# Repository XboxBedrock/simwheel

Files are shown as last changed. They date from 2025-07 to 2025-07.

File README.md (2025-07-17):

# Custom Simracing FFB Wheel

Hi! This is a custom-made Force Feedback Simracing steering wheel, made to somewhat resemble the 2019 Mercedes AMG F1 steering wheel, although not a direct replica. It is made using a hoverboard motor to save costs, and has a screen on the controller for the true F1 experience. For those who may not know what Force Feedback is, it's the usage of a motor to resist the motion of the player, to more closely mimic racecar steering, as the steering column in a racecar offers significant resistance to the driver. Generally this results in higher steering accuracy as humans are very good at gauging pressure accurately compared to distance, so resistance from a wheel helps with that. The wheel itself has a lot of buttons, as does every F1 steering wheel, to allow the driver to enable functions like pit lane steering limiter, etc. I am using keyswitches for a nice shifter experience, and a rotary encoder clutch pedal.

The premade setups you can get at this pricepoint do not offer the same selection of button and screen, and are lacking in torque (Often 2-3 Nm), so that made me want to make a much more capable wheel. There is significant complexity as the hub, wheel, and quickconnect all have to be designed. Overall I am a simracing fan and have always wanted to have a setup like this, but have been outpriced by the $700+ market rates, and figured this could be a great way to use my cad and pcb experience.

## Software

I intend to use a mix of the OpenFFBoard project's software (https://github.com/Ultrawipf/OpenFFBoard) and a small custom serial interface for the buttons and clutch pedal. As such this means you will plug in two USB cables to the computer, one for the wheel control and one for the buttons and clutch and display controller.

## Wiring Diagram

Wiring

This is the full wiring diagram, the display unit will have 2 PCBs hooked up to it for the RPM status lights, and one to hold the shifter keyswitches (which is apart of buttons), as visible in the cad. All of the PCB design files can be found in the [kicad_project](./kicad_project/) folder. Here are the schematics and routing as images for sake of convinience however.

As to not spam this upper section with images, please check the [pcb images section](#pcb-images)

## CAD

All of the CAD was done in fusion 360, and while I *could* export my whole workspace, for the sake of sanity I uploaded the full assembly and just the wheel as two seperate files, the full assembly containing the wheel. Credit to GrabCAD for providing the models for some standard COTS parts (EG. ESP32, Power Supply, Magnetic Encoder Board, etc.).

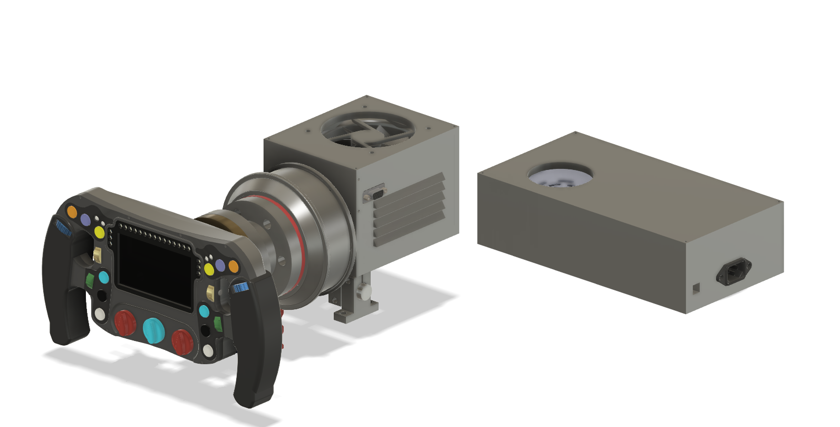
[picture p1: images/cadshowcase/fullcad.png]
full cad

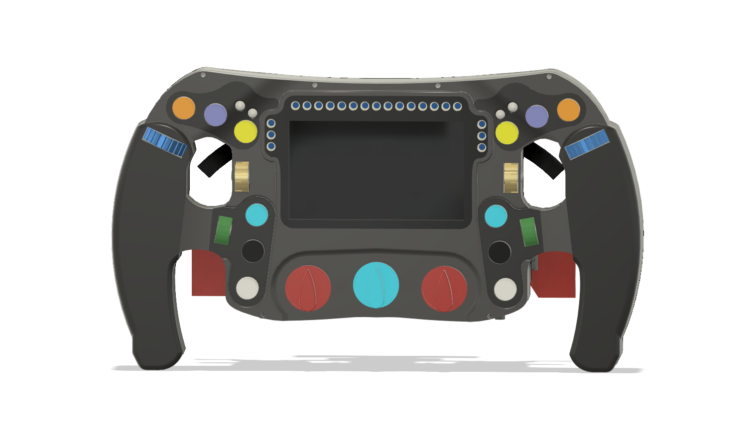
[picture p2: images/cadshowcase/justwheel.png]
Just Wheel


## BOM

|Name |Price |Qty  |Expenditure|FIELD5|Link |Notes: |
|---|---|-----|---|---|---|---|
|Hoverboard |$50 |1 |$50 | |https://www.ebay.com/itm/316843156432 | |
|Ballbearings |$5.45 |1 |$5.45 | |https://www.amazon.com/0-236-Precision-Chrome-Steel-Bearing/dp/B07L8MLK2N/ | |
|Springs |$5.30 |1 |$5.30 | |https://www.amazon.com/uxcell-Compression-Spring-Stainless-Length/dp/B0C33CQ5LN/ | |
|Tactile Switch Buttons 12mm |$0.06 |20 |$1.11 | |https://lcsc.com/product-detail/Tactile-Switches_Megastar-ZX-QC1212-7-5CJ_C7470190.html?s_z=n_12mm%2520button | |
|Rotary Encoder |$1.77 |12 |$21.24 | |https://www.digikey.com/en/products/detail/bourns-inc/PEC11R-4225F-S0024/4499659 |Not in stock on LCSC, no similar models instock either|
|Neopixel Indiv |$4.95 |1 |$4.95 | |https://www.adafruit.com/product/1938 |Only adafruit has in stock and/or sells :( |
|WS2812B |$0.05 |30 |$1.47 | |https://lcsc.com/product-detail/RGB-LEDs-Built-in-IC_XINGLIGHT-XL-5050RGBC-WS2812B_C2843785.html?s_z=n_ws2812b | |
|470 Resistor |$0.00 |100  |$0.19 | |https://lcsc.com/product-detail/Chip-Resistor-Surface-Mount_YAGEO-RC0805FR-0710KL_C84376.html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 | |
|0.1uF Cap |$0.00 |100  |$0.46 | |https://lcsc.com/product-detail/Multilayer-Ceramic-Capacitors-MLCC-SMD-SMT_YAGEO-CC0805KRX7R9BB104_C49678.html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| |
|MX Blue |$1.25 |2 |$2.50 | |https://www.digikey.com/en/products/detail/cherry-americas-llc/MX1A-E1NN/40084 |Not in stock on LCSC, no similar models instock either|
|M3 Screw Assortment |$9.99 |1 |$9.99 | |https://www.amazon.com/Assortment-Stainless-Replacement-Machine-Fastener/dp/B0BMQFHDBH/ | |
|M5 Screw + Nuts |$9.99 |1 |$9.99 | |https://www.amazon.com/Assortment-Machine-Stainless-Washers-Threaded/dp/B0DFWW9DZK/ | |
|4.3"LCD HDMI VGA,Video AV Driver Controller Board,TFT Module Display|$26.79|1 |$26.79 | |https://www.buydisplay.com/4-3-lcd-hdmi-vga-video-av-driver-controller-board-tft-module-display | |
|Carbon Fibre Sticker Wrap |$6.76 |1 |$6.76 | |https://www.aliexpress.us/item/2251832843233677.html | |
|PCB |$15 |1 |$15 | |JLCPCB Cart | |
|SK16 Linear Shaft Holders 4x |$1.18 |1 |$1.18 | |https://www.aliexpress.us/item/2255801037008492.html | |
|SK16 Linear Shaft Holders 2x |$0.99 |1 |$0.99 | |https://www.aliexpress.us/item/3256803971216207.html | |
|16mm Shaft |$7.59 |1 |$7.59 | |https://www.amazon.com/uxcell-Linear-Hardened-Printer-Machine/dp/B0F32ZJCFC | |
|MT6701 + Magnet |$0.99 |1 |$0.99 | |https://www.aliexpress.us/item/3256808951558543.html | |
|OpenFFBoard |$34 |1 |$34 | |https://www.elecrow.com/open-ffboard-stm32f407-usb-interface-only.html | |
|96mm Fan |$8.67 |1 |$8.67 | |https://www.digikey.com/en/products/detail/sunon-fans/MF92252V2-1000U-A99/7652235 |Much to my awe, digikey has it for the cheapest? |
|ODesc 4.2 |$28.99|1 |$28.99 | |https://flipsky.net/products/odesc-v4-2-24v-56v-controller | |
|600W PSU |$29.99|1 |$29.99 | |https://www.amazon.com/BOSYTRO-Switching-Universal-Regulated-Security/dp/B0C53SLDM9/ | |
|C14 Connector |$5.11 |1 |$5.11 | |https://www.digikey.com/en/products/detail/te-connectivity-corcom-filters/1-6609987-4/1306112 | |
|USBC Extension |$2 |1 |$2 | |https://www.walmart.com/ip/onn-USB-C-Extension-Cable-White-6/153042914 | |
|XT90 |11.99 |1 |11.99 | |https://www.amazon.com/Female-Connector-Silicon-RC-Battery/dp/B08L3RS5HP/ | |
|12V Step-Down |8.99  |1 |8.99 | |https://www.amazon.com/VOLRANTISE-Converter-Voltage-Regulator-Transformer/dp/B09WZ5WH8H?th=1 | |
|VGA Connector |9.99  |1 |9.99 | |https://www.amazon.com/uxcell-Connector-Terminal-Mechanical-Equipment/dp/B07LCM71MY/ | |
|VGA Cable |5.28  |1 |5.28 | |https://www.amazon.com/Pasow-Monitor-Cable-Computer-Projector/dp/B08B64KM93/ | |
|ESP32*3 |12.99 |1 |12.99 | |https://www.amazon.com/Development-ESP-WROOM-32-Bluetooth-Microcontroller-Compatible/dp/B0DSZTZKLM/ | |
| | |Total|**$330** | |Willing to incur any extra expense to myself | |

## PCB Images

**Top Lights PCB**
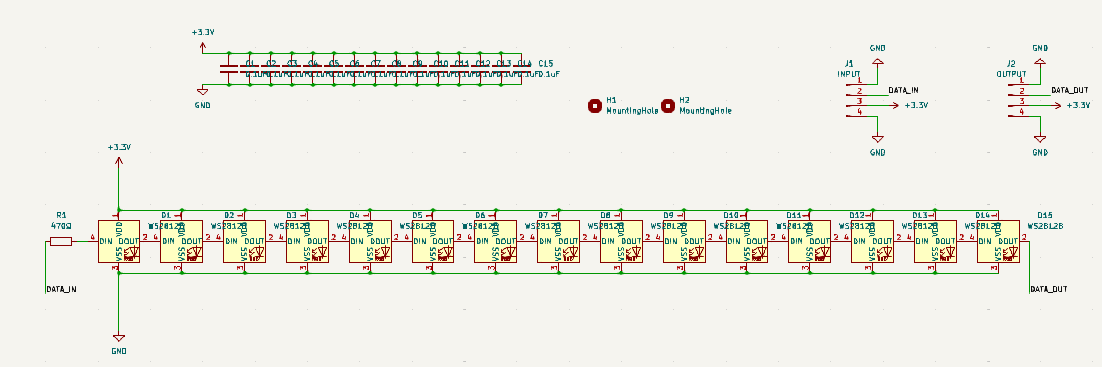
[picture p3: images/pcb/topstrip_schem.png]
Schem
 
PCB

**Safety Lights PCB**
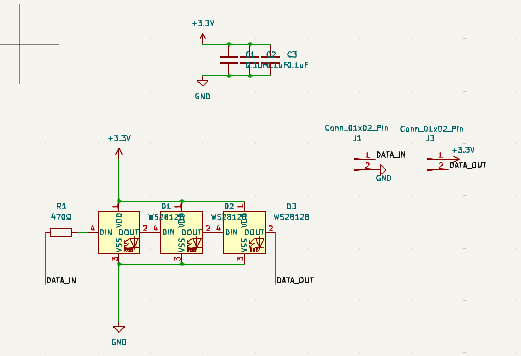
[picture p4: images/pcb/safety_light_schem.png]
Schem
 
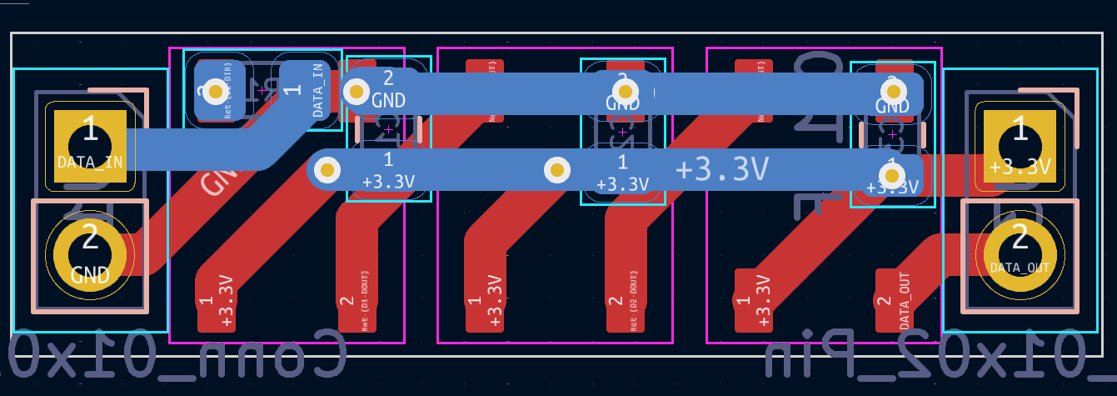
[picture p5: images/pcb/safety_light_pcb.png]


**Shifter PCB**
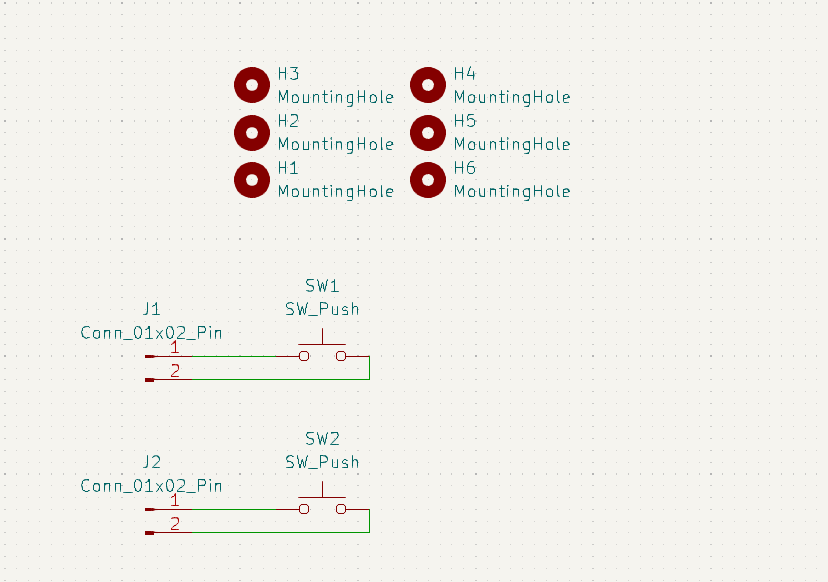
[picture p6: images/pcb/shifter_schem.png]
Schem
 
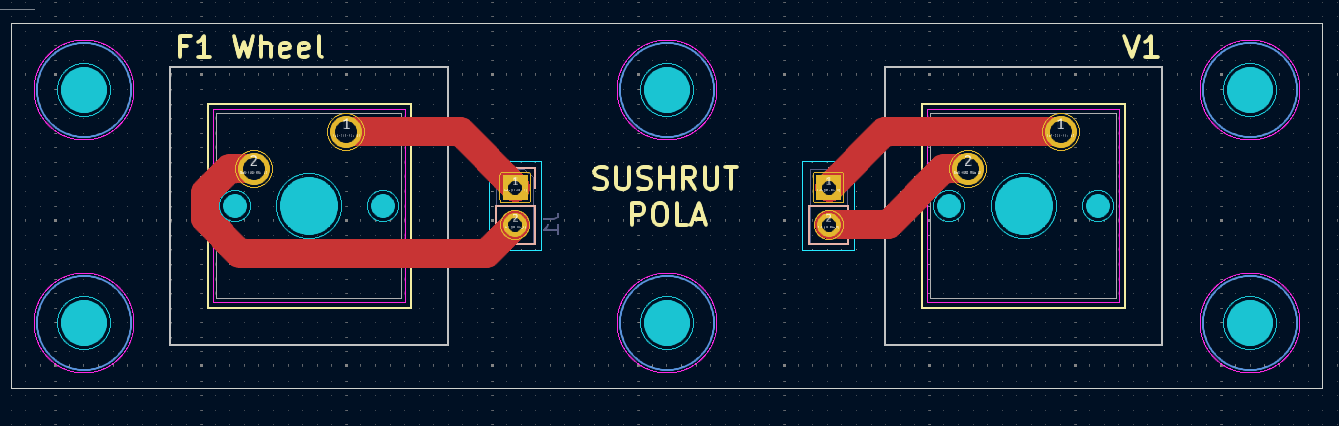
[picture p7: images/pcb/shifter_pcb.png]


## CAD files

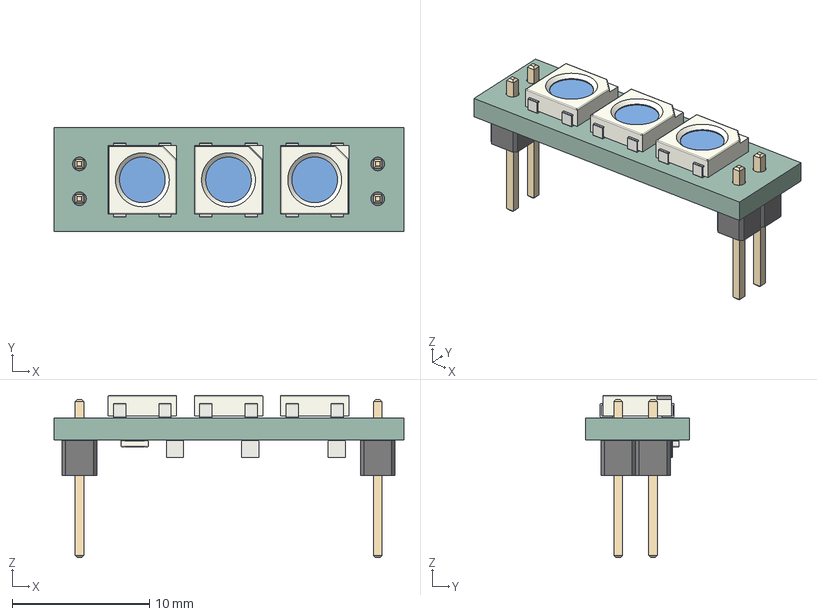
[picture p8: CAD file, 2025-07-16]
kicad_project/safety_light/safety_light/safety_light.step
25.5 x 7.57 x 11.8 mm
LED_WS2812B_PLCC4_50x50mm_P32mm x 3
C_0805_2012Metric x 3
PinHeader_1x02_P254mm_Vertical x 2
R_0805_2012Metric
safety_light_PCB

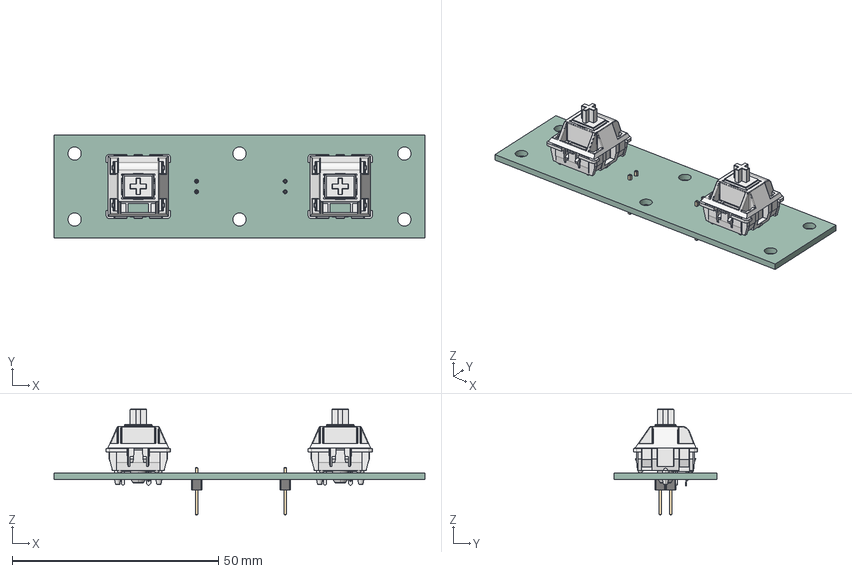
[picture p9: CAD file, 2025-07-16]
kicad_project/shifter/shifter.step
90.0 x 25.0 x 25.7 mm
ASM_MX_ASM_cp x 2
PinHeader_1x02_P254mm_Vertical x 2
shifter_PCB

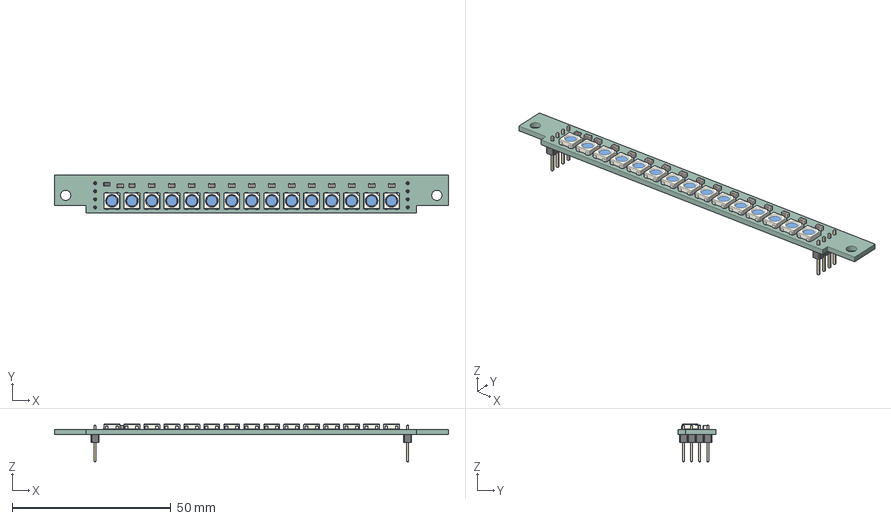
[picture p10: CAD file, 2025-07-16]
kicad_project/topstrip/topstrip.step
124.0 x 12.1 x 11.8 mm
LED_WS2812B_PLCC4_50x50mm_P32mm x 15
C_0805_2012Metric x 15
R_0805_2012Metric
PinHeader_1x04_P254mm_Vertical x 2
topstrip_PCB

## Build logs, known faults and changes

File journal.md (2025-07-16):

---
title: "Force Feedback Simracing Wheel"
author: "Sushrut Pola"
description: "A force feedback simracing steering wheel!"
created_at: "2025-06-06"
---

# Force Feedback Simracing Steering Wheel

**Total Time**: 57.5 Hours

---

Hello there, I am making a Force Feedback Steering wheel to fuel my sim racing addiction. Before I get started, you might be wondering what a "Force Feedback Steering Wheel" even is.

Normally when you turn the steering wheel in a car (even with power steering), you will feel some back force when you turn the wheel. This comes from the friction between the tires and the ground as you turn them. While this friction remains relatively the same on a given surface in a consumer car, this is not the case for racing cars.

Racing cars often use hydraulic power steering instead of electric power steering, which means you directly feel the interaction with the ground. So from how much the steering wheel resists your turning, it is reasonable for an experienced driver to deduce what surface they are on without even looking.

For Formula and Indycars, there is a concept called downforce. Downforce is the amount of force your car is pushed into the ground with. From a basic definition of friction, the more downforce (hence more normal force), the more friction between the tires and the surface. This changes the  way the steering wheel feels significantly.

When we sim race, our goal is to be able to accurately simulate the experience of being a real racecar. This can be achieved by using something called Force Feedback, where a motor attached to the steering wheel resists the motion of the wheel in order to simulate the forces you would feel in a real car.

----

*June 6th, 2025*

**Goals**:
 * Define design constraints and goals
 * Evaluate component choices
 * Possibly get started on a bit of the structural CAD

**Design Constraints**:
 * Ideally be under $350
 * Use components that ship quickly
 * Buildable in a less than 2 week timeframe
 * Is done in a safe manner (I should be confident in leaving this plugged in overnight without issue)

With this in mind, I will now move onto component choices.

In terms of the actual motor for FFB, I believe a hoverboard motor is the best option, this is largely due to its low price for being able to do nearly 15 Nm of torque. This will probably be a dumpster find or ebay find.

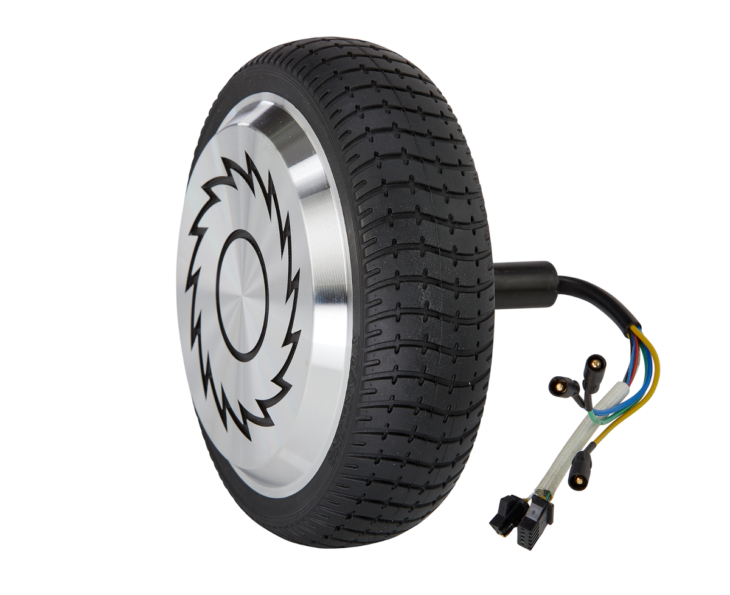
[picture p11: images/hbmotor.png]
A Hoverboard Hub Motor


<i><sup>A hoverboard hub motor<sup></i>

The rest of the parts for the base are largely low cost minutia, mostly 3D printed or standard hardware. However, I do want to use a quick-connect steering hub adapter. This allows for me to switch between wheels, but also requires me to devise a mechanism to quick-disconnect the screen and button cable. That however is a problem for another day. 

In terms of the screen however, I think a 3.5" LCD best suits the f1 style wheel I want. Buttons and switches are fairly COTS components that are easy to find at low cost.

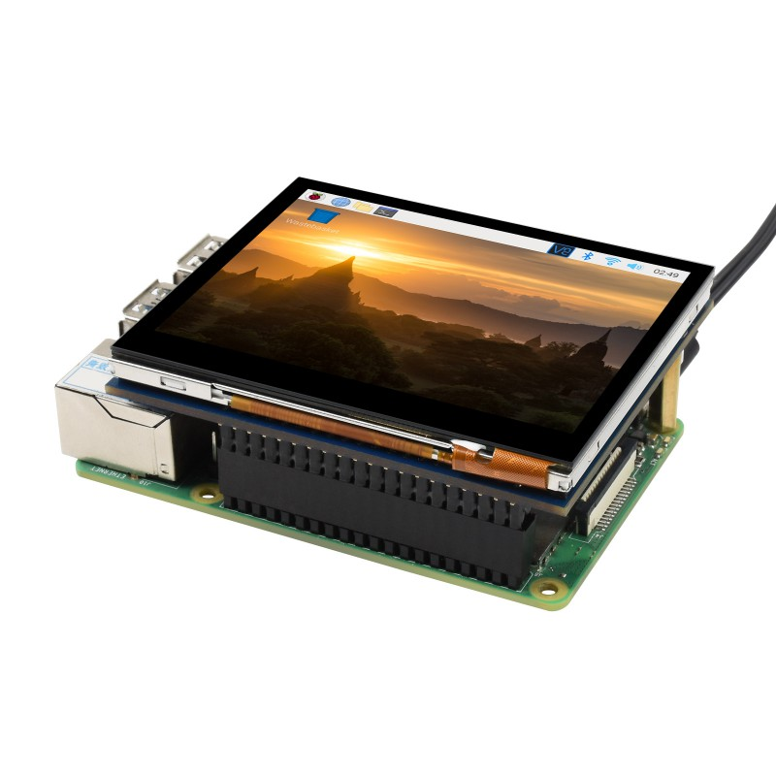
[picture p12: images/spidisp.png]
SPIDISP


<i><sup>A SPI display similar to the one I want to use, they come really cheap<sup></i>

There are some electronic design choices that need to be made, but due to lack of time I will likely do that later.

**Time Spent: 4h**

---

*June 7th, 2025*

One thing this steering wheel needs is a quick connect mechanism. This quick-connect mechanism is what connects the steering wheel to the driver shaft in a manner that can be easily removed. This is very common in racecars and will allow me to easily swap out the wheel later. It will need some 6mm ball bearings for the latch mechanism.

The way it works is a bit convoluted, but in a simple manner there are ball bearings that are pushed in a locking groove, and retracting a collar releases these ball bearings, unlocking the steering wheel and allowing for its removal.

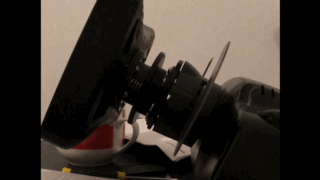
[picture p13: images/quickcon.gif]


<i><sup>A quick connect mechanism similar to what I plan on making<sup></i>

This should be a fairly normal CAD job, however I decided to externalise the cable. While I could integrate data line for the buttons into the connector, I figured that this would be much more of a pain than having an uber long cable. 

Going into fusion, I designed both the male and female parts, lest the collar due to lack of time today.

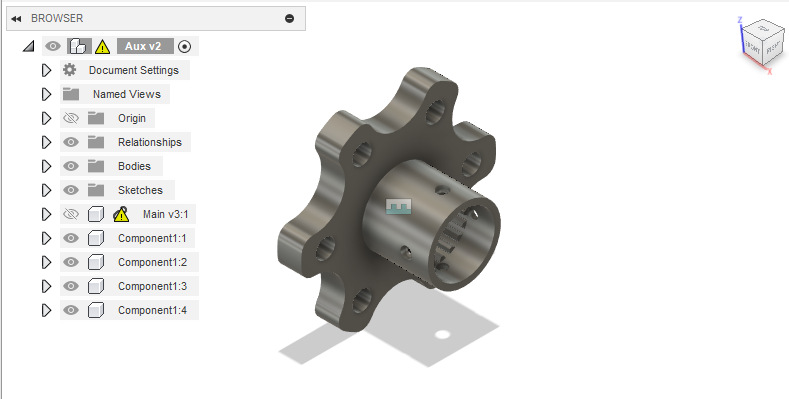
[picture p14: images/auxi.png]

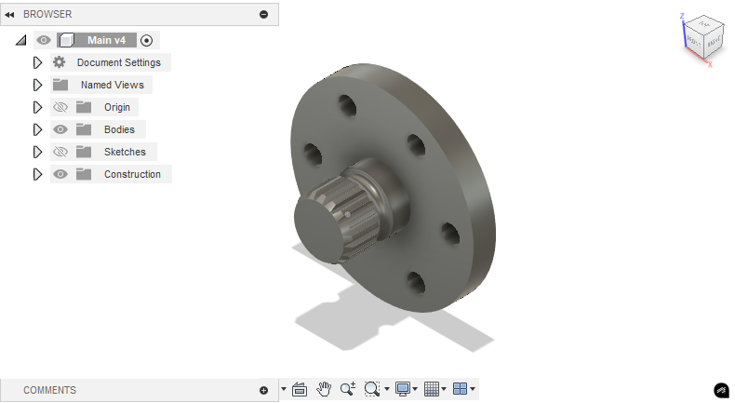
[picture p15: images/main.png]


**Time Spent: 4h**

---

*June 8th, 2025*

It has come time to finish the full quick-connect assembly. I designed the retaining collar today. This keeps the 6mm ball bearings that lock in the wheel in place. Using spring tension, it will hold the bearings with a step, and then the bearings will release when pushed in the back position. The springs used are 6mm diameter wtih 15mm length.

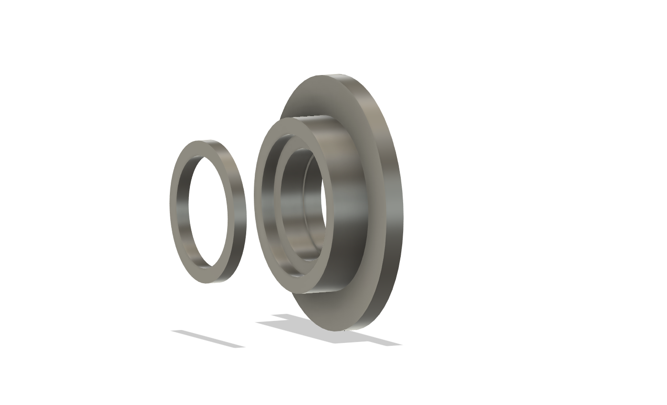
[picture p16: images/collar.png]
collar

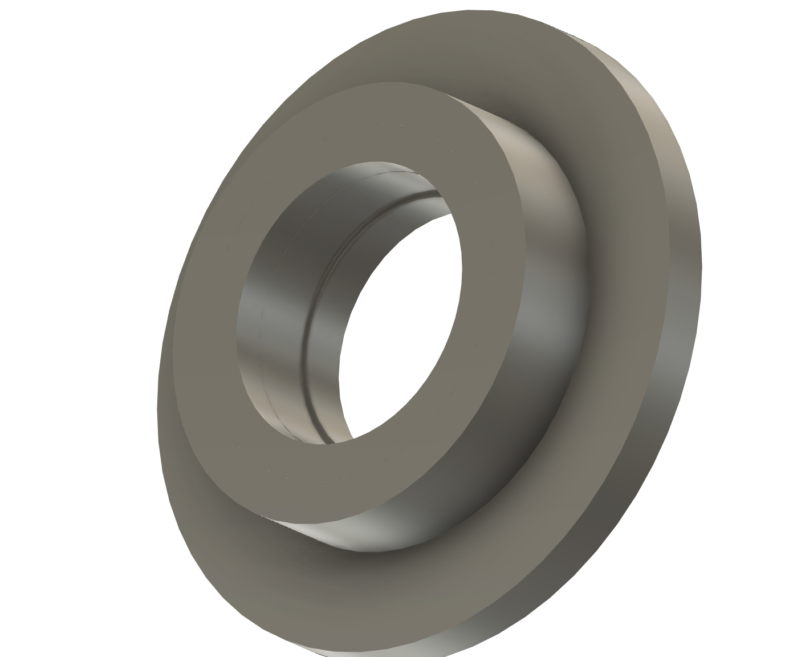
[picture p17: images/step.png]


You can see the little step on the inside, indicating the portion of the collar where the ballbearings are secured in.

I then put it togheter in a final assembly with the ballbearings and the springs, composing the entire quick connect with some color<sup>TM</sup>

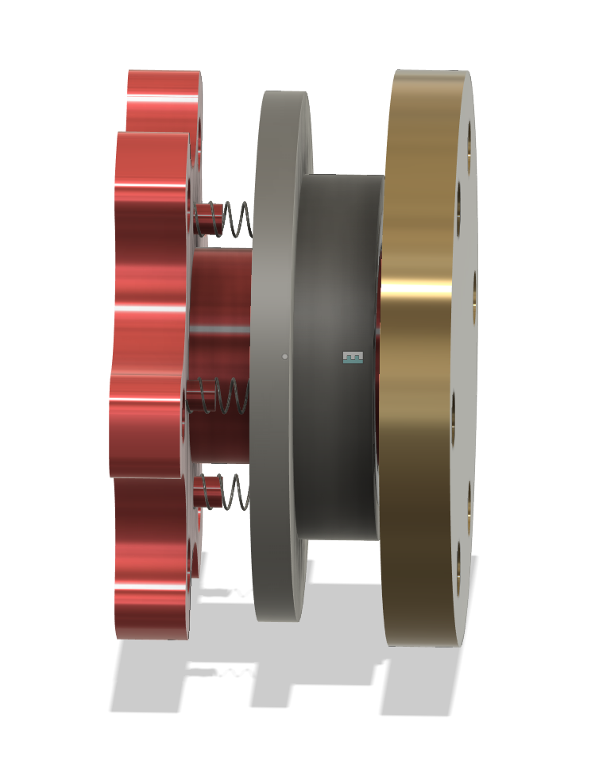
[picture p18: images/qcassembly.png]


This is the full quick connect assembly, so I will move onto the wheel tomorrow

**Time Spend: 2.5h**

---
*June 11th, 2025*

Now, I must get started on the wheel. I am planning on making a clone of the Mercedes F1 Wheel (pictured below). I like the open grip design a lot compared to the closed grip designs that other teams have. 

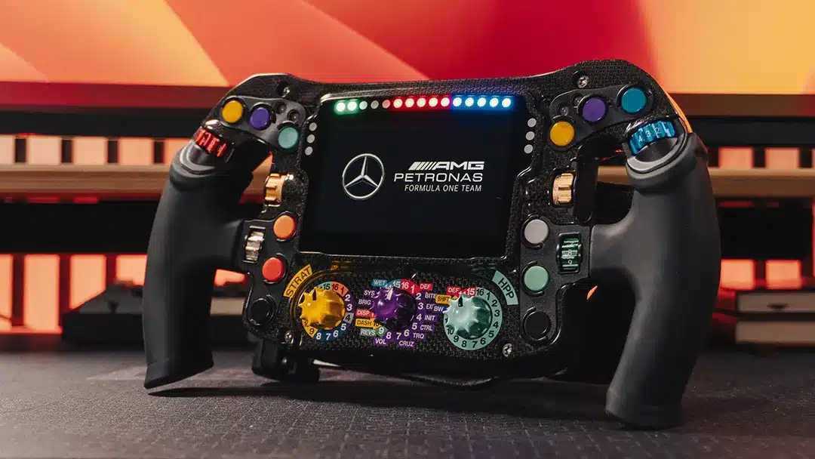
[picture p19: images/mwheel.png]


For the sake of my own sanity, I will probably omit some of the geometry but I aim to make all the buttons functional, which will be an undertaking to say the least. In terms of electronics, the lights are 5mm diameter so something like the Adafruit 5mm neopixels will work great. To avoid a severe case of overscoping, I will not make the knobs function except the center 3 as I really do not use them.

I actually looked up the dimensioning for the wheel to find nothing, and it turns out it is a 4.3 inch display. I will change to using a 4.3 inch SPI display at this point due to this discrepancy with my earlier estimate. I spent the day sketching out the major features of the wheel, I will deal with the actual modelling tommorow. 

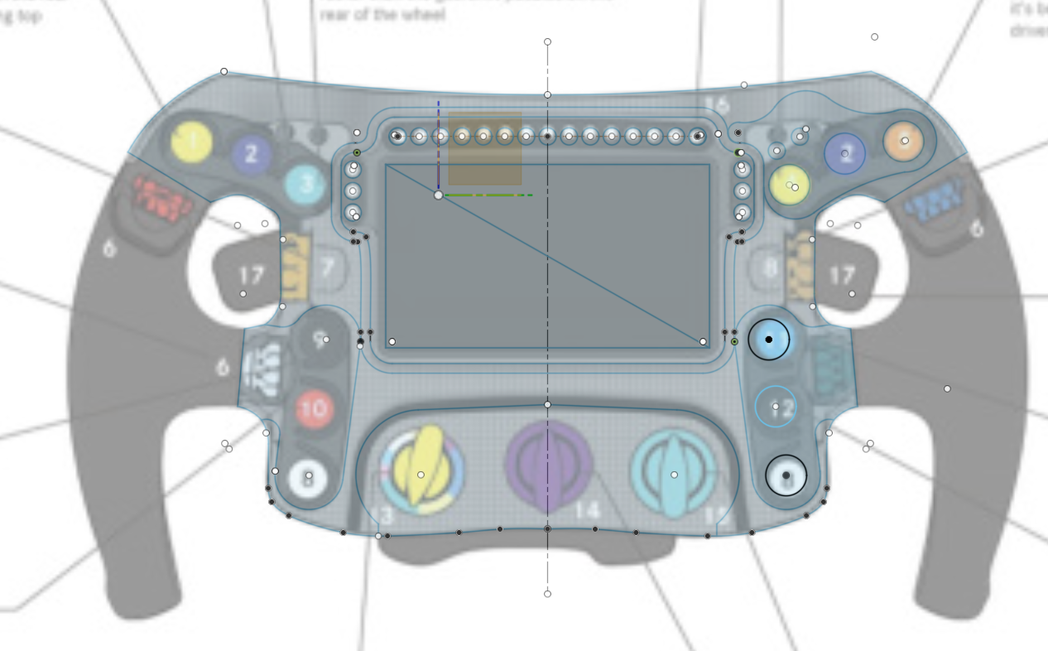
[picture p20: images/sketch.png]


You may notice some of the geometry is not mirrored, I gave up mirroring halfway through and figured I can just mirror once we are in the realm of 3d, saving me plenty time.

**Time Spent: 2h**

---
*June 16th, 2025*

Oooh boy its been a long day. I decided to just sit down and get a lot done. The entire front shell of the controller has been completed and partially the back shell. 

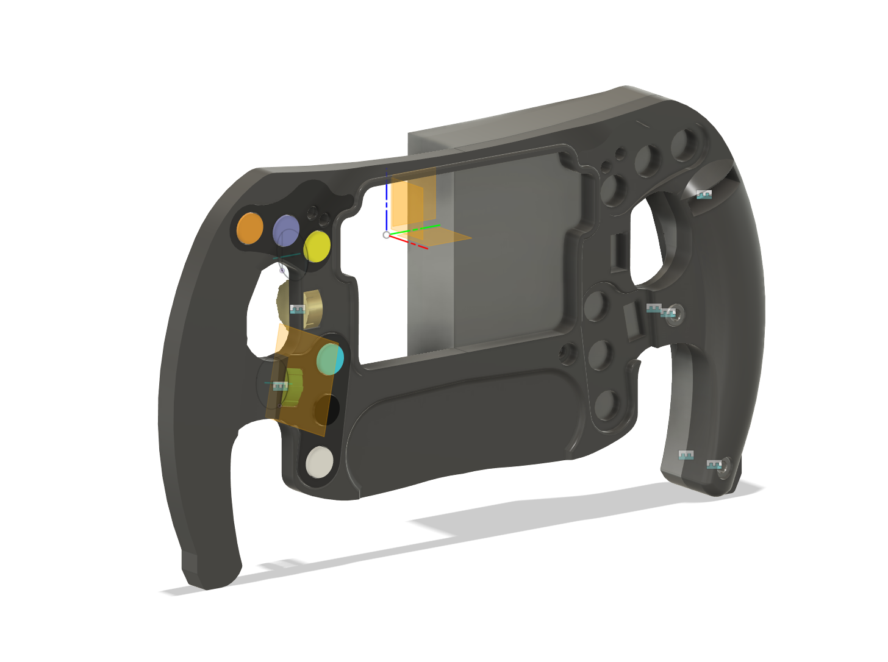
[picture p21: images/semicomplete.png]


The front shell with buttons and rollers is completed, knobs are pending for the time being. One of the things I did do was do the curve geometry for part of the back shell, so now I can get the chance to work on the shifter piece and mounting mech. The largest part left is hollowing pieces so I can fit in electronics, and making a mounting piece.

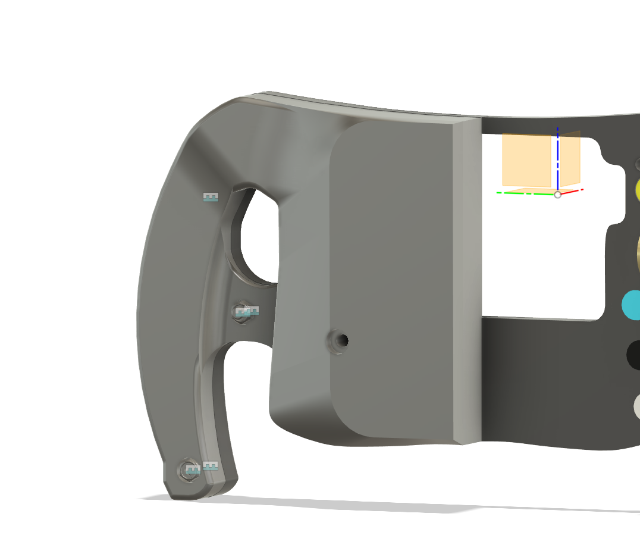
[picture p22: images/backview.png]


Just a back view

In terms of electronics, it looks like we're gonna be in for a wild ride. I want to make a custom PCB just for the LED strips since I *really* do not want to be dealing in terms of individual LED wiring (and I want to use neopixels), besides that I want to use perfboard since space is not of the greatest concern. In terms of the MCU on the inside, I remain unsure. I think using an esp32 for all of this is probably my best bet however, if not a PI 0 (cooling go die).

Keeping power delivery in mind, I think I'm better off with the esp32 since I want data and power on the same coiled cable.

**Time Spend: 10h**

---
*June 17th, 2025*

I'm gonna take a break from CAD for a bit since it has been exhausting me, and look at electronics for a second

The goal today is to make the neopixel strip at the top, similar to https://www.adafruit.com/product/2869#technical-details 

The idea is to make a compact PCB that can be hand-soldered. Here is a schematic of what i'm thinking.

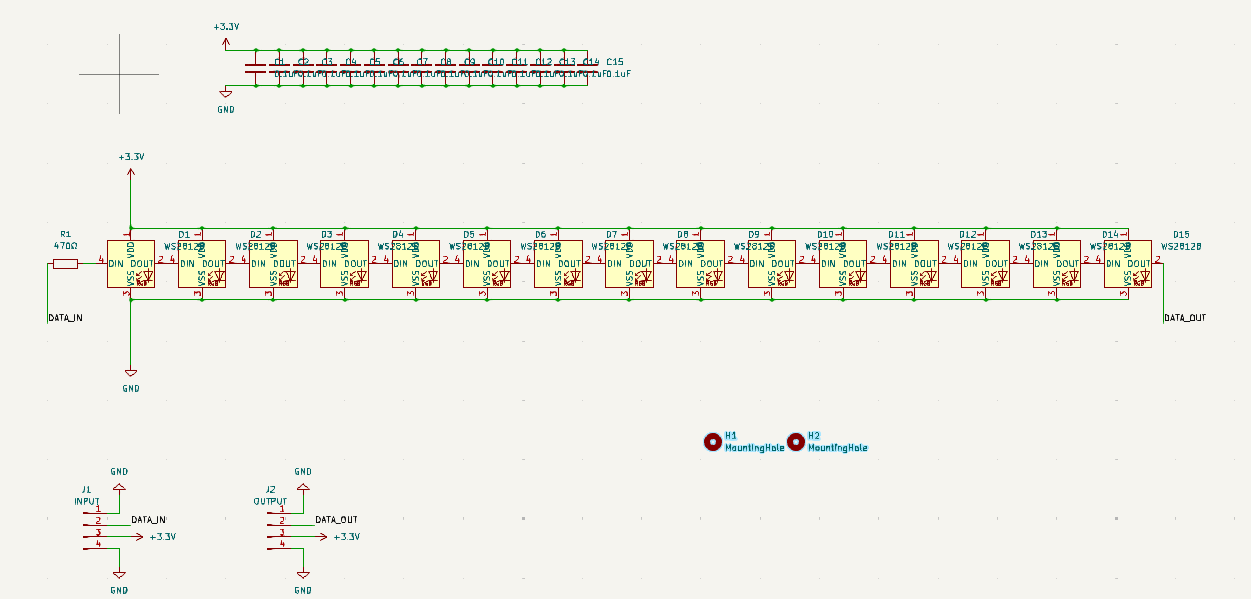
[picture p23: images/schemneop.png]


This is what the routing looks like, it is two sided to make it as compact as possible. I am happy with how compact I got it to be.

SPIDISP

I also made a small version for the safety lights on either side

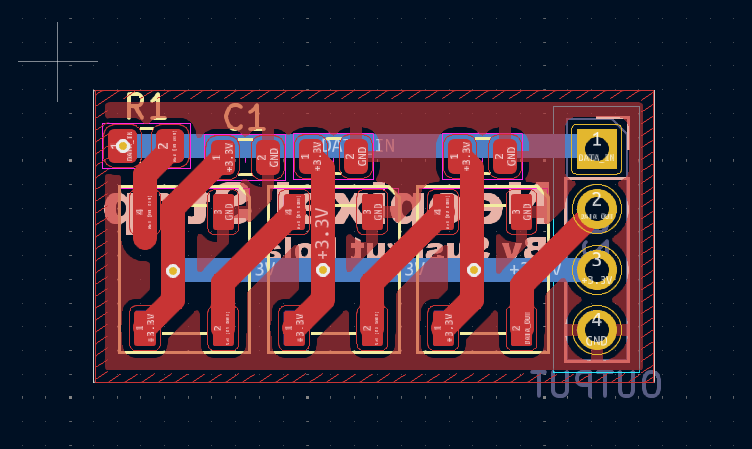
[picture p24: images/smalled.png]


Now, I will integrate this into the actual frame of screen in CAD. The PCB has m3 screw holes for this mounting reason

I probably want to use a LCD Display like this https://www.amazon.com/Waveshare-4-3inch-Capacitive-Microcontroller-Dual-Core/dp/B0CTG8LZ6Z/, it has dedicated control which is needed as one esp32 can't handle button inputs and display. I will likely link this with the control board using something like i2c.

No official word, but this probably mounts with m3 screws or something of the sort, realistically this is just a make a box that fits and use hot glue job. 

**Time Spend: 6h**

---
*June 20th, 2025*

Today, I finished embedding the buttons and encoders into the front panel. For encoders I decided to use the https://www.adafruit.com/product/377 (found cheaper on digikey listed as PEC11R-4215F-S0024). These things are small yet cheap which is a hard balance to find with rotary encoders. I have heard good things too about the tactile feel. Seems like a no-brainer. (I need to cut a few mm off the shaft, but SHHHH)

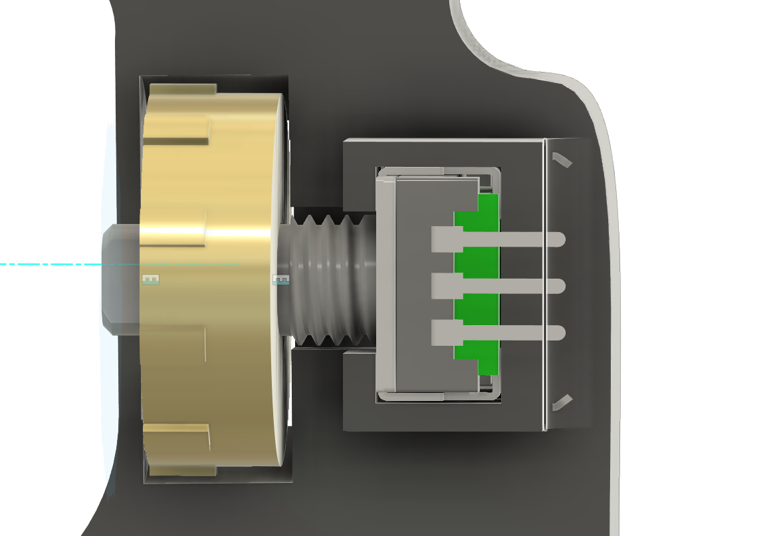
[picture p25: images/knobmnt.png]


One thing I will do is hot glue in plain neopixel LEDs (the 5mm kind, can be found at https://www.adafruit.com/product/1938) for the two status indicators near the top of the controller.

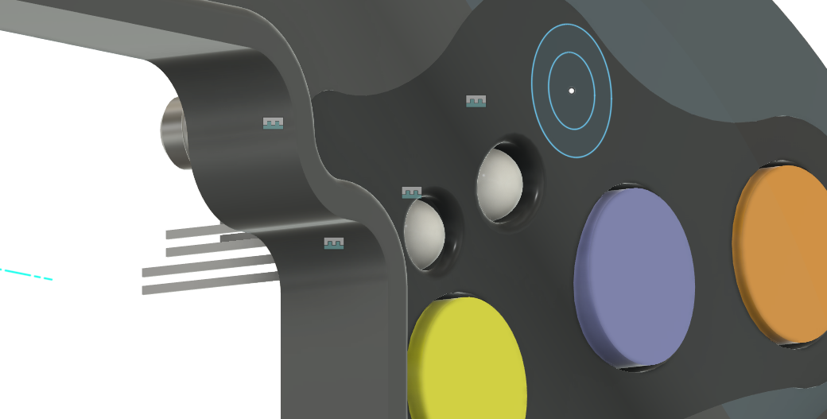
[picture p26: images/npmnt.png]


I am using 12mm tactile buttons for the clicks, they are extremely cheap and just work.

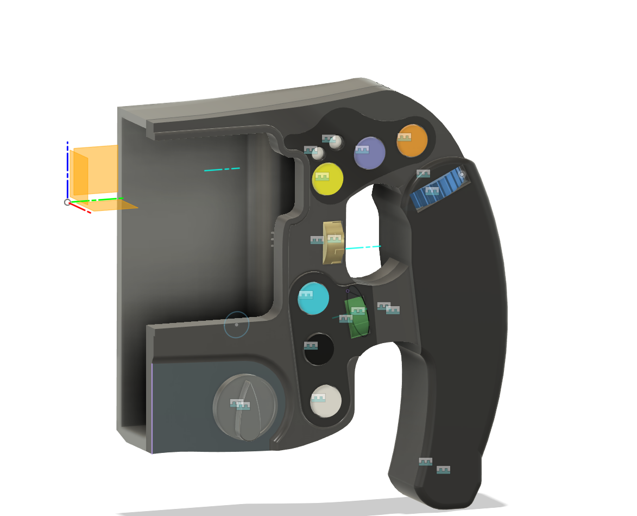
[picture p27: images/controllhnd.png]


Here is what the mounting looks like 

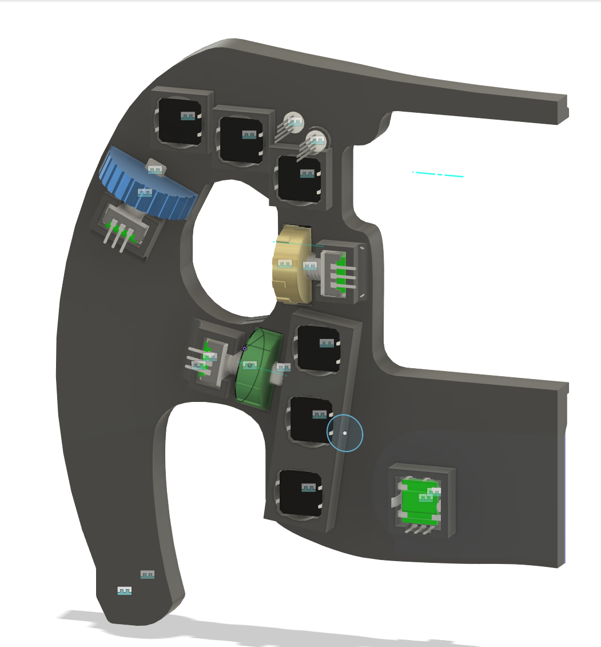
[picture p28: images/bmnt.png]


Now, I am onto finishing the controller itself with the shift paddle and clutch paddles. I am probably best off starting with the clutch paddles since they are a slightly simpler design. The whole thing will be held togheter by a number of m3 screws

The clutch paddle has been completed, and features a somewhat ergonomic design with rotary encoder and cable passthrough

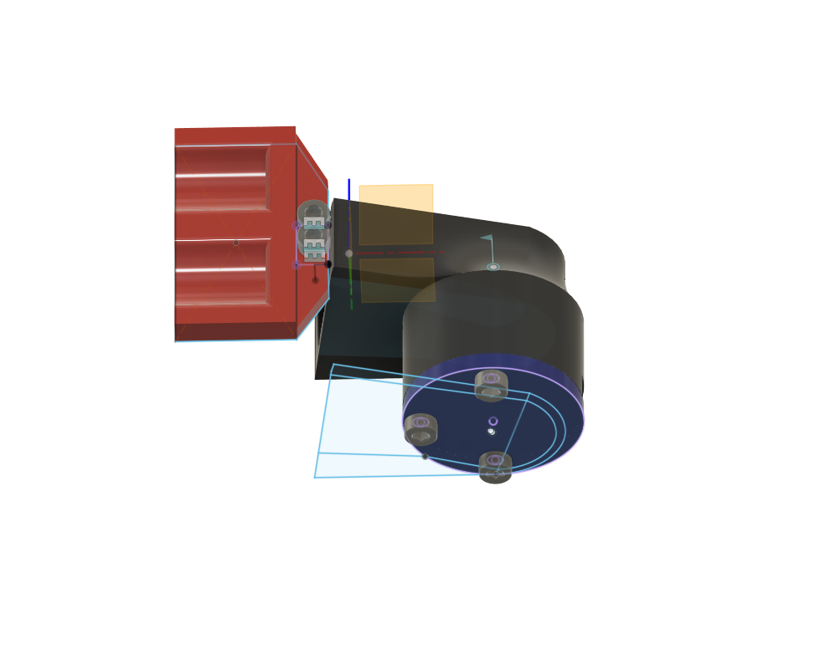
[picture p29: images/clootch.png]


Thats where i'll call it a day

**Time Spent: 12h**

---
*June 28th, 2025*

After a long break, i'm back at it in full swing

I need to get the screen integrated with the LED panels. My old esp32 powered screen seems like a poor choice, so I am getting a new one. This screen from buydisplay.com seems like a good choice, but I need some sort of board to control it via SPI or i2c. 

https://www.buydisplay.com/low-cost-4-3-inch-480x272-tft-lcd-display-w-optl-capacitive-touch-screen

Adafruit has the RA8875 Board but its expensive and out of stock :sob:

But then I found this sweet deal, https://www.buydisplay.com/4-3-lcd-hdmi-vga-video-av-driver-controller-board-tft-module-display

For 28 dollars, I had what was a control board with VGA interface. While I may have preferred SPI or i2c, since ESP32s come cheap I can just dedicate one to VGA and talk to it over i2c or SPI

After a bit of fitzing around, I got the screen to go in, I still need to figure out a mount for the rest of of the electronics

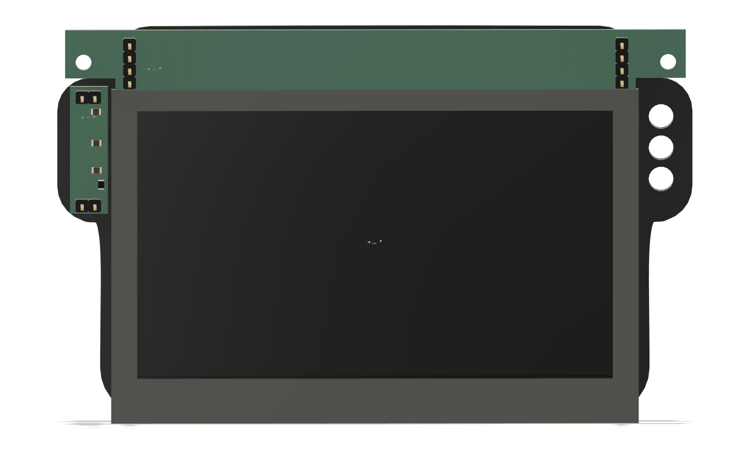
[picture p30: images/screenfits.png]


With the screen integrated, I am getting even closer to completion

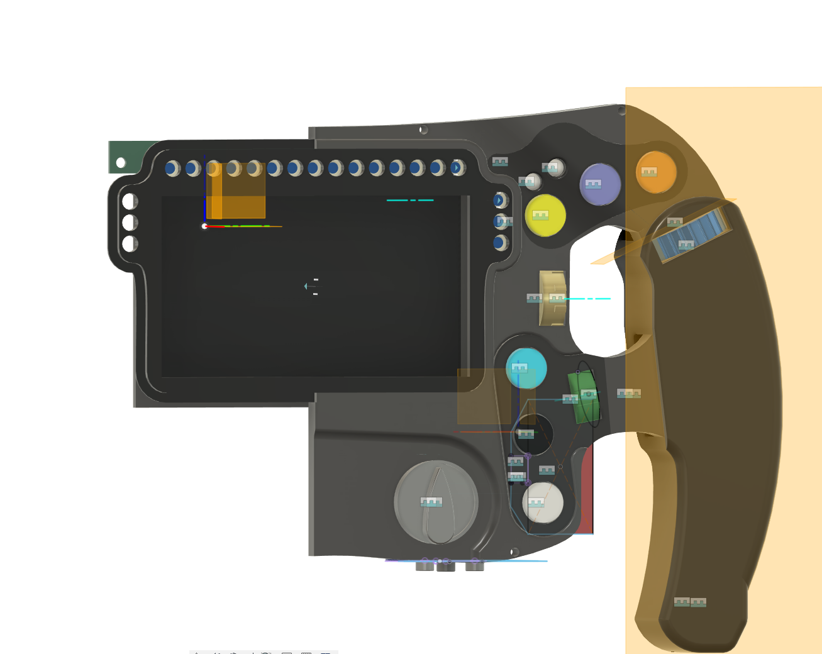
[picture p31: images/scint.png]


**Time Spent: 6h**

---
*July 2nd, 2025*

Today, I'm working on the sequential shifter and then moving to the wheelbase. 

I decided to use Cherry MX Blues for the switches. I will still add my own springs but these switches are very nice and give the tactile feel I want for shifting. I will make a PCB to give me ease of mount with these switches.

The PCB was very simple to make, just keyswitch and m3 screwholes. Could I have wired this by hand, probably. But this is a very cheap and simple mount

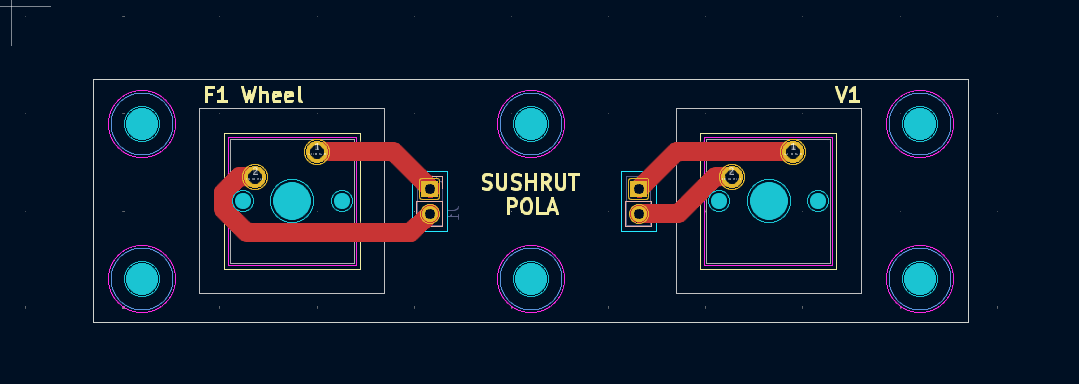
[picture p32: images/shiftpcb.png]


Then I mounted it, which was a relatively simple job

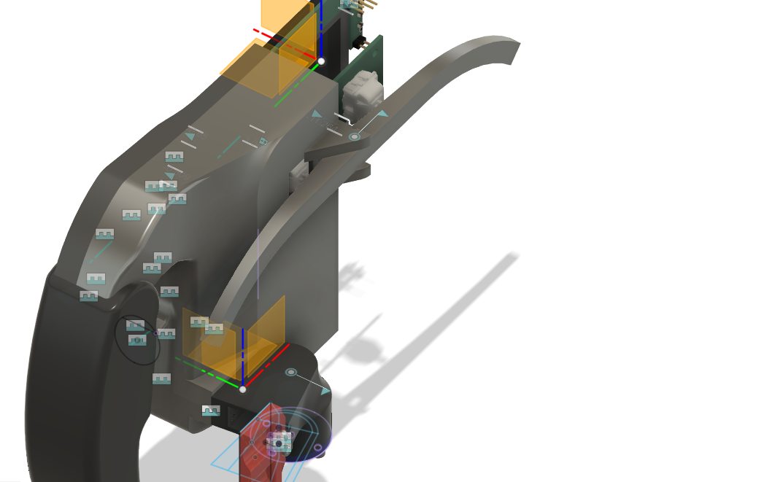
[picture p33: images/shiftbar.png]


The inside is mounted with a little standoff system.
By now, I am ready to make the other half appear, and I can finish the electronics and add the port then.

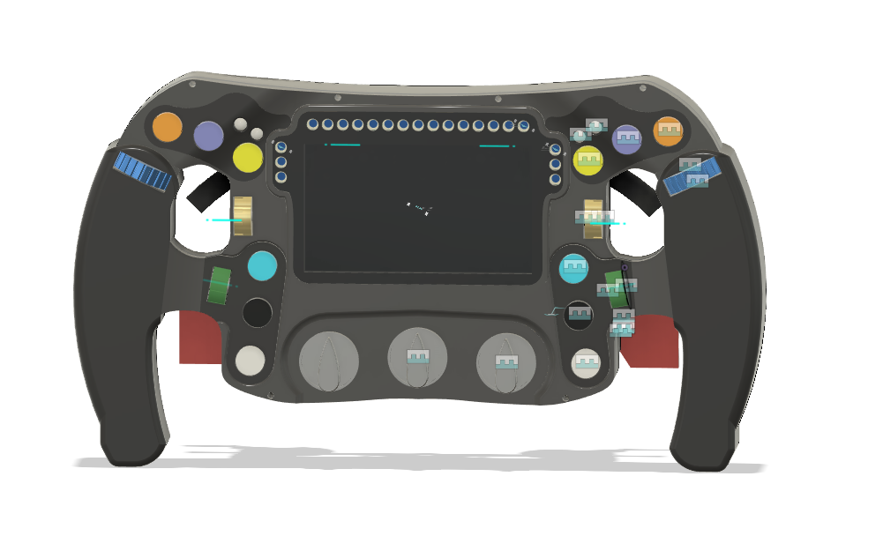
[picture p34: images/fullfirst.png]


And thats the controller in its full glory. I will circle back to wiring once the wheelbase is done.

**Time Spent: 6h**

---

*July 3rd, 2025*

One day before funny fireworks day and I'm back to work on this guy. With the controller largely done I first want to mount the hub before I do the base itself.

I have mounted it and reinforced the back plate to make sure force feedback dosen't become forced dissasembly for wheel.

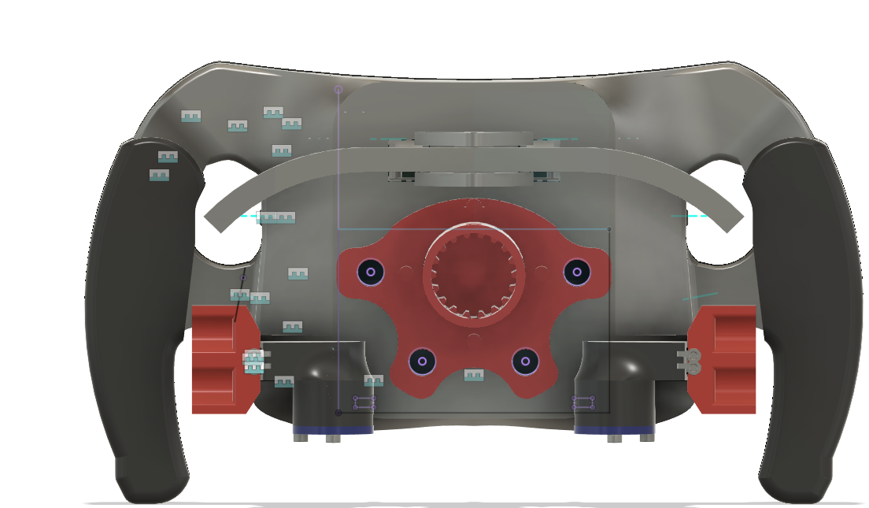
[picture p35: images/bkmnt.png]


By now, I can just plop it on the hoverboard wheel, it will screw in by drilling 6 holes into the wheel

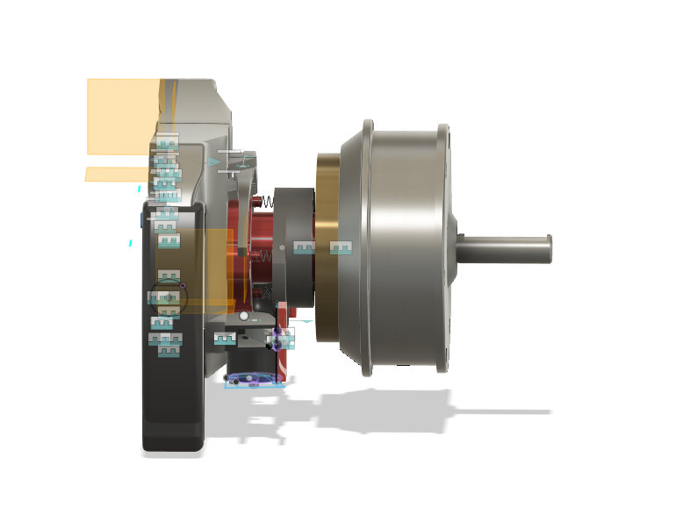
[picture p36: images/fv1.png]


It fits nicely. Now, I found out that SK16 linear shaft holders will fit the hoverboard wheel shaft perfectly. Using these holders I will hold the shaft in place to the baseboard. I am thinking a PCB mount board is a decent idea. But I need to fix some stuff about the mechanicals for the electronics to work. 
https://www.amazon.com/uxcell-Aluminum-Clamping-Support-Diameter/dp/B07QS8LKZ8/

I am also needing to add an magnetic encoder assembly. Which was fairly easy to design as it just pins the magnet inside the motor shell.

This is for the MT6701 encoder, the 18x15mm kind

I also need to interate the Open FFBoard, as it is the best open source device for the purpose, and the board isn't *too* expensive. https://www.elecrow.com/open-ffboard-stm32f407-usb-interface-only.html

**Time Spend: 4h**

---
*July 11th, 2025*

I need to add a fan to the device to prevent overheating of the OpenFFB board, so I decided to go with a standard PC fan, 92x25mm https://www.digikey.com/en/products/detail/sunon-fans/MF92252V2-1000U-A99/7652235

And to work with the odrive, I need an ODESC motor controller, this is largely for the hoverboard motor as it draws literally insane amounts of current.
https://flipsky.net/products/odesc-v4-2-24v-56v-controller

For the actual device power, I need to add a 600W power supply to avoid overload, and 24V is the input I need.
https://www.amazon.com/BOSYTRO-Switching-Universal-Regulated-Security/dp/B0C53SLDM9/

I also need a C14 power connector
https://www.amazon.com/GELRHONR-Inline-Wiring-Stripped-Appliances/dp/B09M83L8FS/

And this extension for the esp32
https://www.amazon.com/Faracent-Extension-Charging-Nintendo-Touchbar/dp/B0BX3X548D/

And here is the XT-90 power connector I need for my battery
https://www.amazon.com/Meimom-Female-Connector-Silicon-Battery/dp/B0DBV45VBY?gQT=2

I know product listing is boring, but bear with me for a second, I'll get to some interesting stuff soon

In terms of connecting the wheel buttons and mcu to the base, I want to use serial over a VGA connector. As stupid as this may sound, it actually works really well and is reliable, even for 12V power delivery.
https://www.amazon.com/uxcell-Connector-Terminal-Mechanical-Equipment/dp/B07LCM71MY/

Since the supply is 24V and the display is 12V, I need this converter to let me supply 12V to the wheel, which the display driver will step down for everything to wire to!
https://www.amazon.com/VOLRANTISE-Converter-Voltage-Regulator-Transformer/dp/B09WZ5WH8H

I also need both a coiled vga cable for the wheel and one to splice for the internal display.
https://www.amazon.com/Pasow-Monitor-Cable-Computer-Projector/dp/B08B64KM93/

Here is a final wiring diagram of what wiring will look like:
Wiring

This is somewhat complex but manageable, the two ESP32s are used for the fact that I fear one may not be enough to handle the sheer IO throughput needed for the display, and could lag out the buttons. This is why the display has its own ESP.

Here is the completed cad with all electricals integrated.

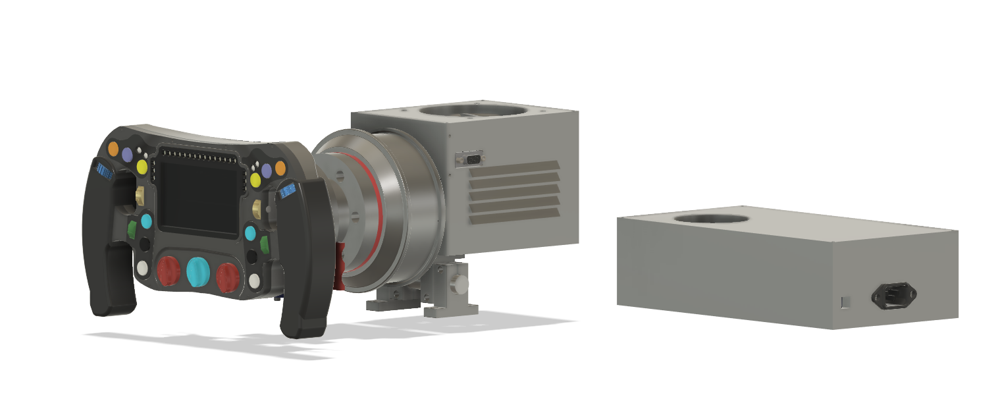
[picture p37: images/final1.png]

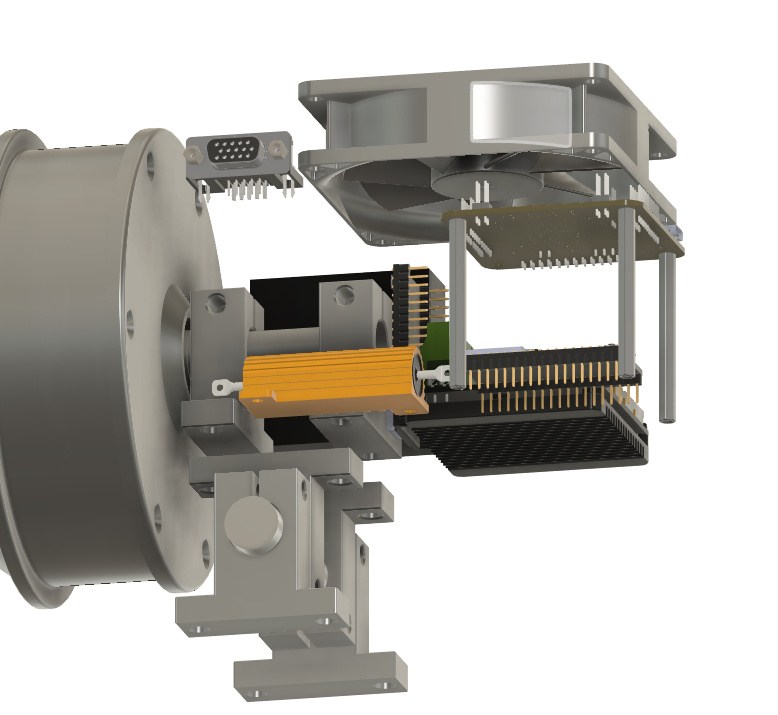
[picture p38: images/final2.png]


With this, I am very certain that the project has reached a practical conclusion, I am now going to make a BOM and submit.

**Time Spent: 5h**

---

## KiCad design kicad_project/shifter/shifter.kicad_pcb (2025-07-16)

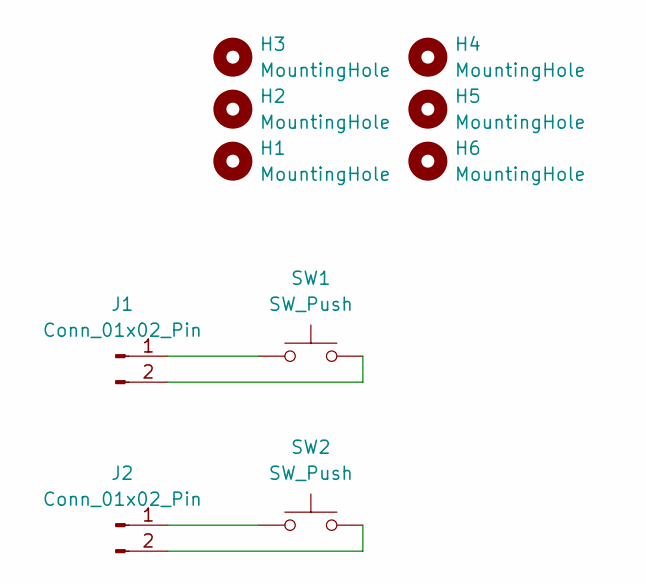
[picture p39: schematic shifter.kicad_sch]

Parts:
H1, H2, H3, H4, H5, H6: MountingHole; MountingHole_3.2mm_M3
J1, J2: Conn_01x02_Pin; PinHeader_1x02_P2.54mm_Vertical
SW1, SW2: SW_Push; SW_Cherry_MX_1.00u_PCB

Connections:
unnamed: J1.1, SW1.1
unnamed: J1.2, SW1.2
unnamed: J2.1, SW2.1
unnamed: J2.2, SW2.2

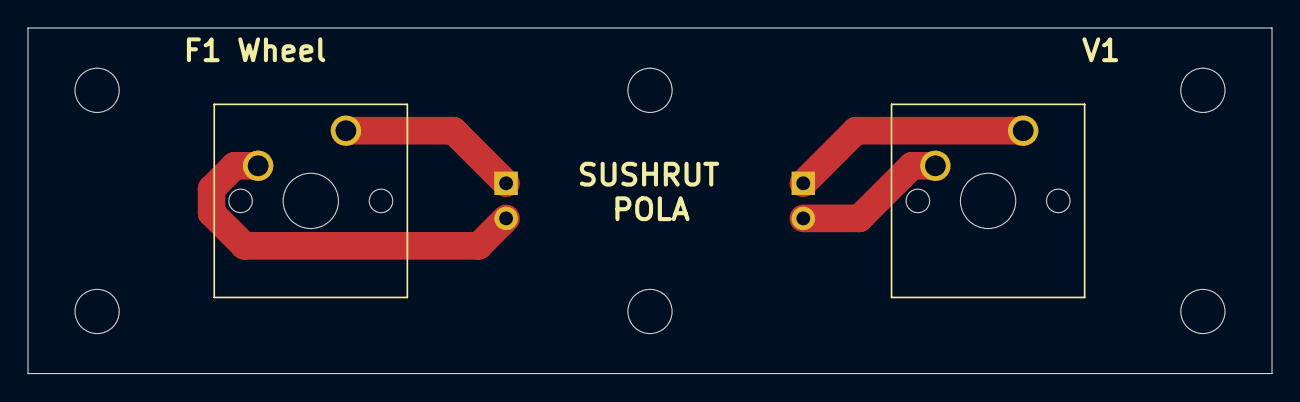
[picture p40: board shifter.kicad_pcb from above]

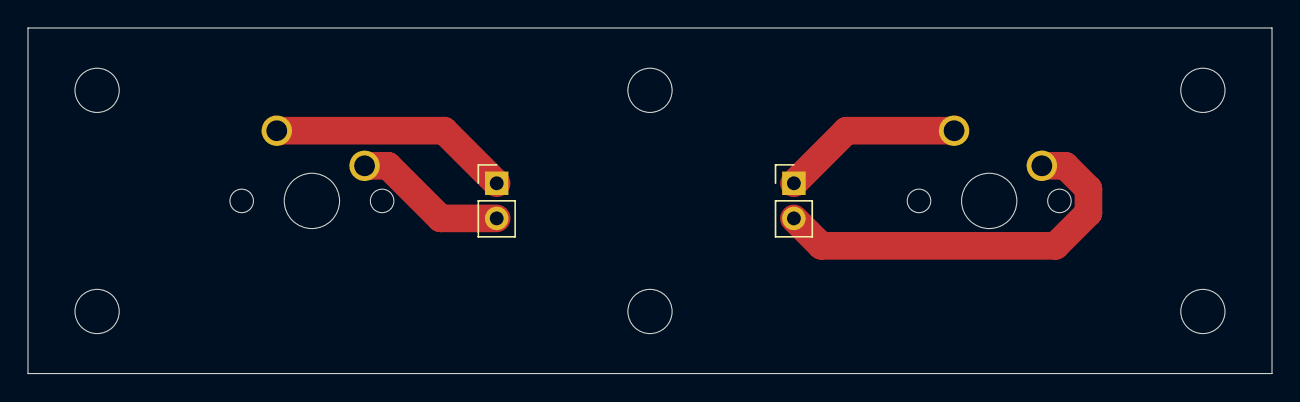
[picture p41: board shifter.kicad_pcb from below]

Board: 2 copper layers, 90.0 x 25.0 mm, 10 parts (2 on the bottom side), 4 nets.

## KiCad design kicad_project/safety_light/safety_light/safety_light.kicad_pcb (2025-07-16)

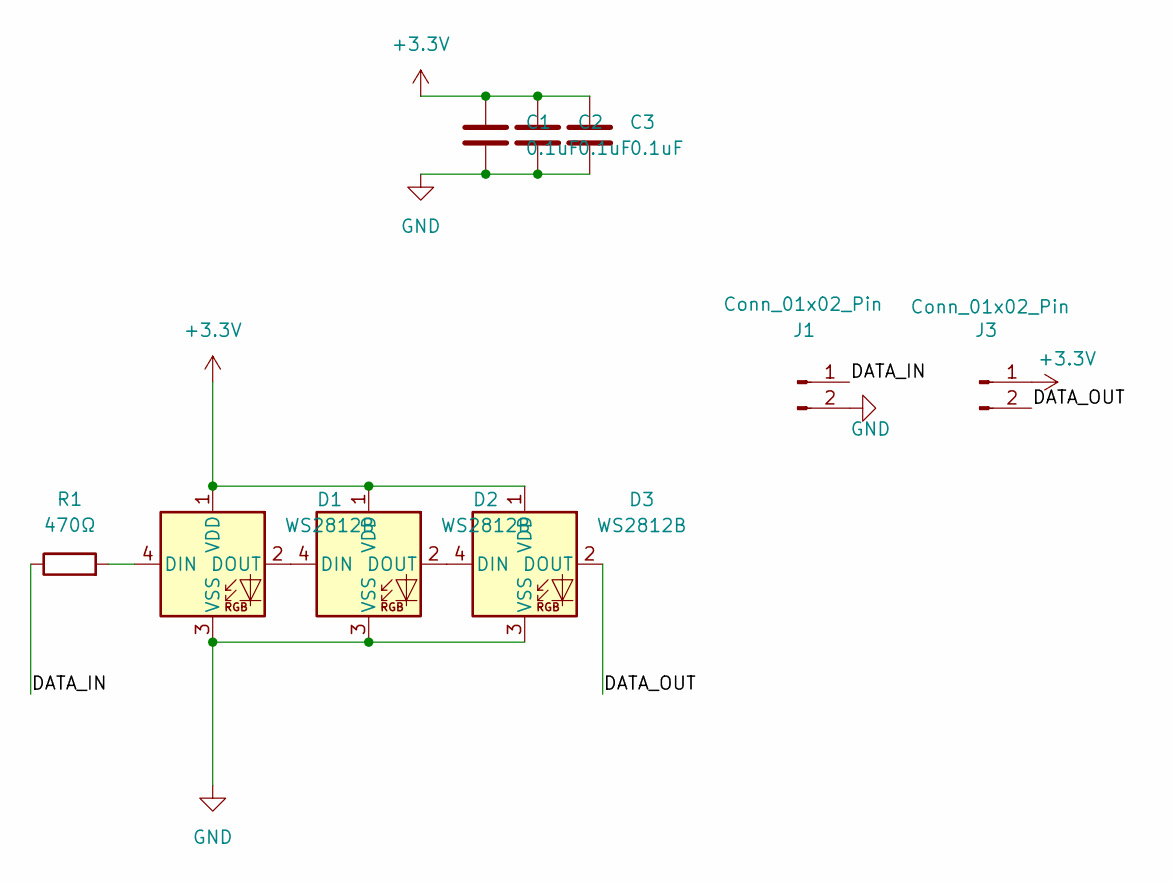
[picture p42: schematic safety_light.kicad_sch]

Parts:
C1, C2, C3: 0.1uF; C_0805_2012Metric
D1, D2, D3: WS2812B; LED_WS2812B_PLCC4_5.0x5.0mm_P3.2mm
J1, J3: Conn_01x02_Pin; PinHeader_1x02_P2.54mm_Vertical
R1: 470Ω; R_0805_2012Metric_Pad1.20x1.40mm_HandSolder

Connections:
+3.3V: C1.1, C2.1, C3.1, D1.1 (VDD), D2.1 (VDD), D3.1 (VDD), J3.1
/DATA_IN: J1.1, R1.1
/DATA_OUT: D3.2 (DOUT), J3.2
GND: C1.2, C2.2, C3.2, D1.3 (VSS), D2.3 (VSS), D3.3 (VSS), J1.2
unnamed: D1.4 (DIN), R1.2
unnamed: D1.2 (DOUT), D2.4 (DIN)
unnamed: D2.2 (DOUT), D3.4 (DIN)

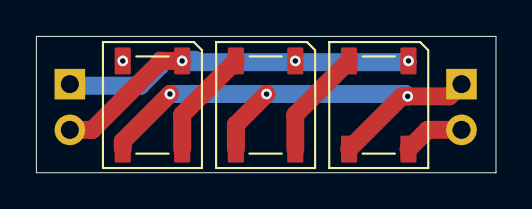
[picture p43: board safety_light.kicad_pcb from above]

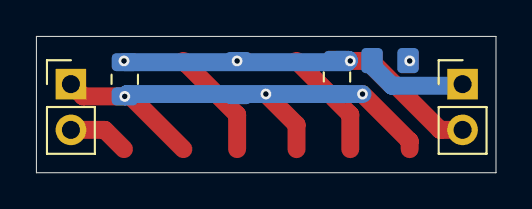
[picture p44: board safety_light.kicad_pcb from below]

Board: 2 copper layers, 25.5 x 7.6 mm, 9 parts (6 on the bottom side), 7 nets.

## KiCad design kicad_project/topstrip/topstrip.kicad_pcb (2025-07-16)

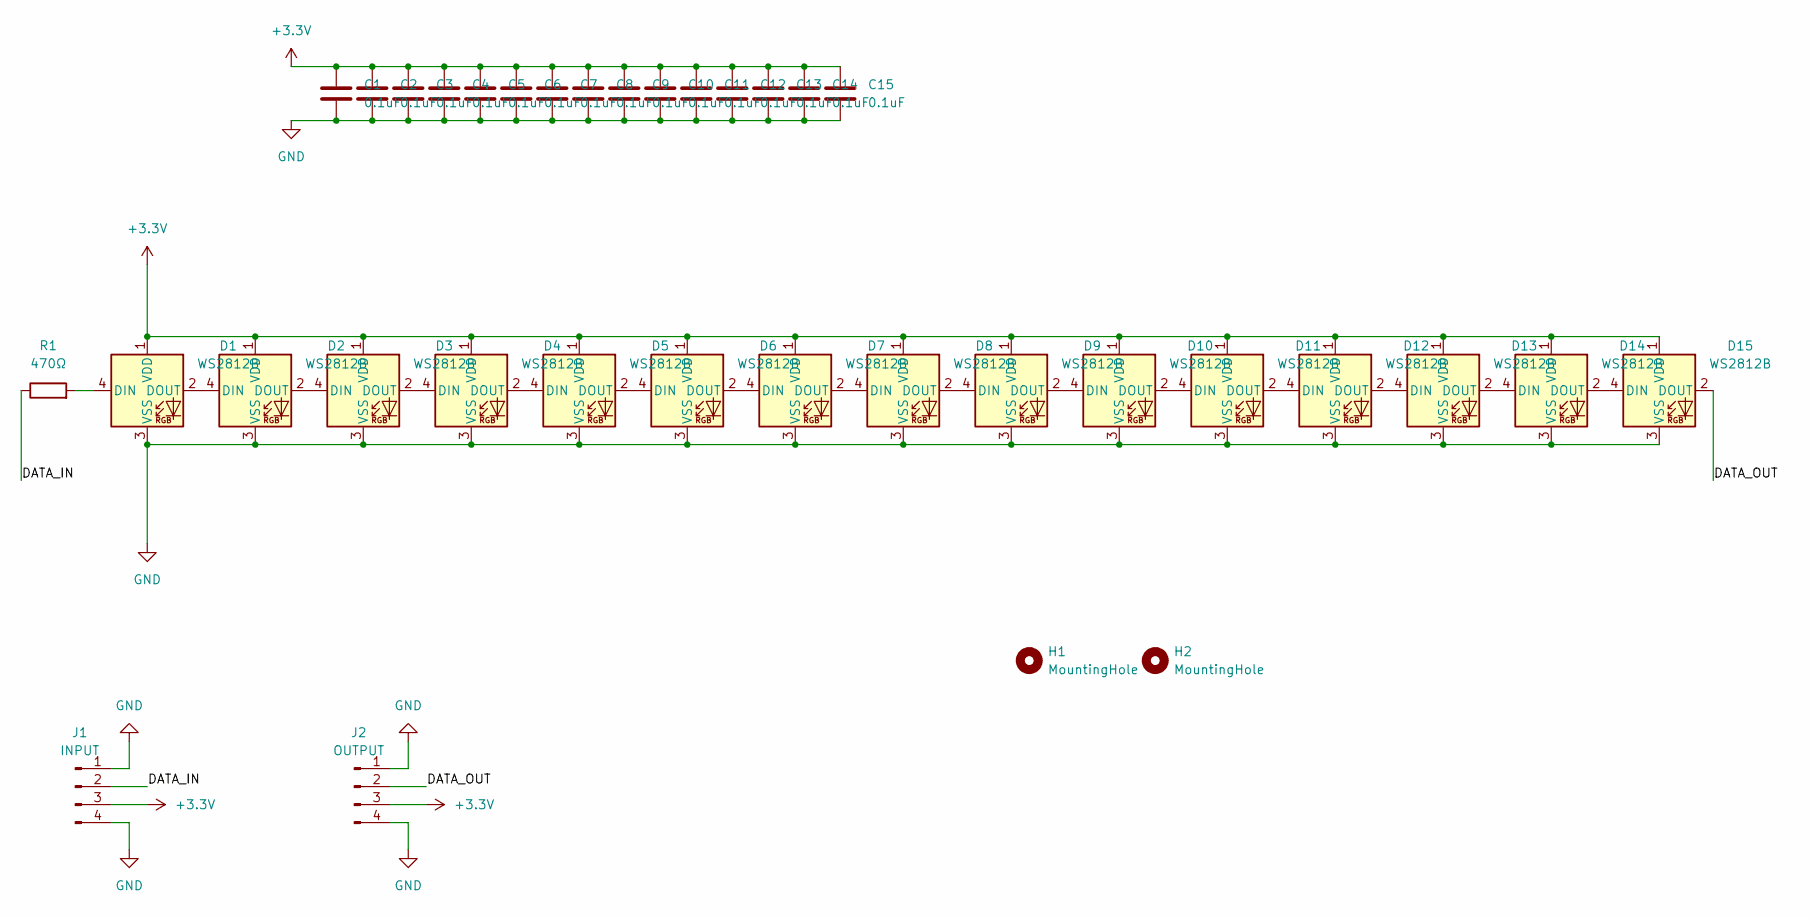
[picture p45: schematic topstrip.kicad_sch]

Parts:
C1, C2, C3, C4, C5, C6, C7, C8, C9, C10, C11, C12, C13, C14, C15: 0.1uF; C_0805_2012Metric
D1, D2, D3, D4, D5, D6, D7, D8, D9, D10, D11, D12, D13, D14, D15: WS2812B; LED_WS2812B_PLCC4_5.0x5.0mm_P3.2mm
H1, H2: MountingHole; MountingHole_3.2mm_M3_DIN965
J1: INPUT; PinHeader_1x04_P2.54mm_Vertical
J2: OUTPUT; PinHeader_1x04_P2.54mm_Vertical
R1: 470Ω; R_0805_2012Metric_Pad1.20x1.40mm_HandSolder

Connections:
+3.3V: C1.1, C2.1, C3.1, C4.1, C5.1, C6.1, C7.1, C8.1, C9.1, C10.1, C11.1, C12.1, C13.1, C14.1, C15.1, D1.1 (VDD), D2.1 (VDD), D3.1 (VDD), D4.1 (VDD), D5.1 (VDD), D6.1 (VDD), D7.1 (VDD), D8.1 (VDD), D9.1 (VDD), D10.1 (VDD), D11.1 (VDD), D12.1 (VDD), D13.1 (VDD), D14.1 (VDD), D15.1 (VDD), J1.3, J2.3
/DATA_IN: J1.2, R1.1
/DATA_OUT: D15.2 (DOUT), J2.2
GND: C1.2, C2.2, C3.2, C4.2, C5.2, C6.2, C7.2, C8.2, C9.2, C10.2, C11.2, C12.2, C13.2, C14.2, C15.2, D1.3 (VSS), D2.3 (VSS), D3.3 (VSS), D4.3 (VSS), D5.3 (VSS), D6.3 (VSS), D7.3 (VSS), D8.3 (VSS), D9.3 (VSS), D10.3 (VSS), D11.3 (VSS), D12.3 (VSS), D13.3 (VSS), D14.3 (VSS), D15.3 (VSS), J1.1, J1.4, J2.1, J2.4
unnamed: D1.4 (DIN), R1.2
unnamed: D1.2 (DOUT), D2.4 (DIN)
unnamed: D2.2 (DOUT), D3.4 (DIN)
unnamed: D3.2 (DOUT), D4.4 (DIN)
unnamed: D4.2 (DOUT), D5.4 (DIN)
unnamed: D5.2 (DOUT), D6.4 (DIN)
unnamed: D6.2 (DOUT), D7.4 (DIN)
unnamed: D7.2 (DOUT), D8.4 (DIN)
unnamed: D8.2 (DOUT), D9.4 (DIN)
unnamed: D9.2 (DOUT), D10.4 (DIN)
unnamed: D10.2 (DOUT), D11.4 (DIN)
unnamed: D11.2 (DOUT), D12.4 (DIN)
unnamed: D12.2 (DOUT), D13.4 (DIN)
unnamed: D13.2 (DOUT), D14.4 (DIN)
unnamed: D14.2 (DOUT), D15.4 (DIN)

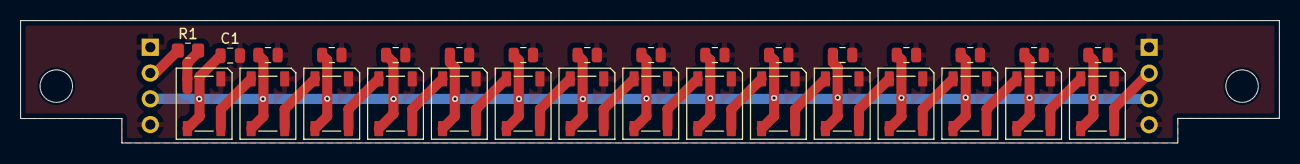
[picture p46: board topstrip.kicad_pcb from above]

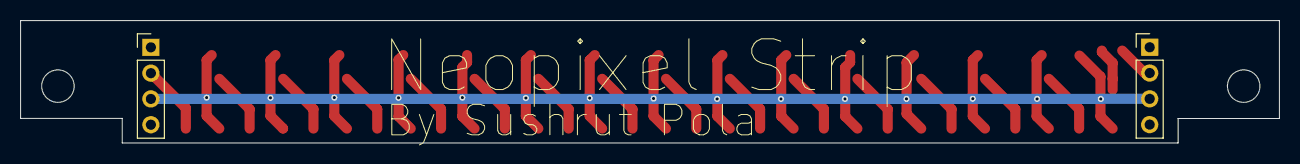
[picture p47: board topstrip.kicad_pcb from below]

Board: 2 copper layers, 124.0 x 12.1 mm, 35 parts (2 on the bottom side), 19 nets.
